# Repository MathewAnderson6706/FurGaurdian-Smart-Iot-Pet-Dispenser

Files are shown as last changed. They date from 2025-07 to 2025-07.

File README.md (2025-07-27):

# Automatic Pet Food Dispensor using RasperryPi 4 
Title Page (1st odd page not numbered, X.0 sections begin on odd pages, otherwise double sided and numbered)  
## Declaration of Joint Authorship   
### Task Distribution
We, FurGuardian, confirm that this breakdown of authorship represents my contribution to the work submitted for assessment and my contribution is my own work and  is expressed in my own words. Any uses made within the Technology Report of the works of any other author, separate to the work group, in any form (ideas, equations, figures, texts, tables, programs), are properly acknowledged at the point of use. A list of the references used is included.
| Task | Mathew | Justin | Tevadi | Zane |
|---|---|---|---|---|
| **3D Print / Container** | 50% | 10% | 10% | 30%  |
| **Mobile Programming** | 30% | 50% | 10% | 10%  |
| **Hardware Connectivity**  | 45% | 25% | 15% | 15%  |
| **Hardware Programming** | 40% | 40% | 10% | 10%  |
| **Documentation** | 25% | 25% | 25% | 25%  |

[^1]
[^1]: Technology Report Guidelines. OACETT, Revised September 2022. Available at: https://www.oacett.org/getmedia/5ad707d7-f472-4b24-a7fe-f34e270b0c41/2022_TR_Guidelines_-_Updated_Version_-_Sept_2022.pdf
## Proposal/Project Specifications   
[Link to proposal](wk01proposal.md).   
## Executive Summary   
Our project focuses on enhancing pet care for owners who are away during the day. It features a **smart pet food dispenser** equipped with advanced functionalities:

- **Camera**:  
  Allow owners to interact with their pets remotely, ensuring constant connection and engagement.

- **Infrared Sensor**:  
  Detects pet presence to automate feeding and interaction processes.

- **Stepper Motor**:  
  Dispenses precise portions of food to maintain proper dietary control.

- **solenoid push intermittent**:  
  Enables treat dispensing as an added feature for rewarding and engaging pets.

## Table of Contents

[Declaration of Joint Authorship](#declaration-of-joint-authorship)   
[Proposal/Project Specifications](#proposalproject-specifications)   
[Executive Summary](#executive-summary)   
[Table of Contents](#table-of-contents)   
[List of Figures](#list-of-figures)   

[1.0 Introduction](#10-introduction)   
[1.1 Background](#11-background)   
[1.2 Project Requirements and Specifications](#12-project-requirements-and-specifications)   
[1.3 Project Schedule](#13-project-schedule)   

[2.0 Hardware Development Platform Report/Build Instructions](#20-hardware-development-platform-reportbuild-instructions)  
[2.1 Mathew Anderson-Saavedra/A](#21-student-onea)  
[2.2 Tevadi Brookes/B](#22-student-twob)  
[2.3 Zane Aransevia/C](#23-student-threec)  
[2.4 Justin Chipman/D](#24-student-fourd)  

[3.0 Mobile Application Report](#30-mobile-application-report)  
[3.1 Deliverable 1](https://github.com/Chipman8472/FurGuardian/blob/master/Docs/FurGuardian_Deliverable1_Group8.pdf)  
[3.2 Deliverable 2](https://github.com/Chipman8472/FurGuardian/blob/master/Docs/Deliverable2/FurGuardian_PetWellness_Group8_2.pdf)  
[3.3 Deliverable 3](https://github.com/Chipman8472/FurGuardian/blob/master/Docs/FurGuardian_Deliverable3_Group8.pdf)  
[3.4 Deliverable 4](https://github.com/Chipman8472/FurGuardian/blob/master/Docs/FurGuardian_PetWellness_Deliverable4_Group8.pdf)   
[3.5 Deliverable 5](https://github.com/Chipman8472/FurGuardian/blob/master/Docs/Deliverable%205/FurGuardian_Deliverable5_Group8.pdf)  

[4.0 Integration](#40-integration)  
[4.1 Enterprise Wireless Connectivity](#41-enterprise-wireless-connectivity)  
[4.2 Database Configuration](#42-database-configuration)  
[4.3 Network and Security Considerations](#43-network-and-security-considerations)  
[4.4 Unit Testing](#44-unit-testing)  
[4.5 Production Testing](#45-production-testing)  
[4.6 Sustainability Considerations](#46-sustainability-considerations)  
[4.7 Challenges/Problems](#47-challengesproblems)  
[4.8 Solutions](#48-solutions)  

[5.0 Results and Discussion](#50-results-and-discussion)

[6.0 Conclusions](#60-conclusions)

[7.0 Appendix](#70-appendix)  
[7.1 Firmware Code](#71-firmware-code)  
[7.2 Mobile Application Code](#72-mobile-application-code)  

[8.0 References](#80-references)  

## List of Figures   
[Figure 1: Gantt Chart](#figure-1-gantt-chart)  

## 1.0 Introduction   
This project was undertaken to complete Humber Polytechnics CENG-355 Captsone project. The problem we are trying to solve is pet owners being away from their animals and not being able to interact or tend to thier needs while away. This dispensor aims to allow users to both interact with and feed thier pets while away from home. 

In section 1 we will discuss similar products on the market, the project requirements and specifications and the project schedule. In section 2 we will discuss the hardware devevlopment of the project. Section 3 links several reports about the development of the mobile app. Section 4 outlines the integration of the project as a whole.
### 1.1 Background
There are a few players on the market already for pet food dispenosrs. Pet Cube offers good remote pet interaction to keep pets engaged but lacks health information for the animals. Whistle offers good health tracking but lacks remote interaction with the animals. Our product aism to fuze these 2 functions into a single product.
### 1.2 Project Requirements and Specifications
This project has the following requirements.

Hardware:
- Raspberrypi 4
- Infared Sensor
- Solenoid push intermittent
- Stepper motor and a controller
- Camera

Firmware:
- Python dependencies (time, threading, cv2, smbus2, socket, RPI.GPIO, flask, pyrebase, pyngrok)
- Compatable python version

### 1.3 Project Schedule       
###### Figure 1: Gantt Chart     
Gantt Chart 

## 2.0 Hardware Development Platform Report/Build Instructions   
### 2.1 Mathew Anderson-Saavedra/A
[Hardware report](hardware/ceng317reportMathew.md)   
### 2.2 Tevadi Brookes/B   
[Hardware report](hardware/ceng317reportTB.md)   
### 2.3 Zane Aransevia/C   
[Hardware report](hardware/rc522.md)  
### 2.4 Justin Chipman/D   
[Hardware report](hardware/ceng317report.md)   
  
## 3.0 Mobile Application Report   
### 3.1 Deliverable 1
[Mobile Deliverable 1](/tree/main/docs/Deliverable%201)   
### 3.2 Deliverable 2      
[Mobile Deliverable 2](/tree/main/docs/Deliverable%202)   
### 3.3 Deliverable 3      
[Mobile Deliverable 3](/tree/main/docs/Deliverable%203)   
### 3.4 Deliverable 4      
[Mobile Deliverable 4](/tree/main/docs/Deliverable%204)   
### 3.4 Deliverable 5      
[Mobile Deliverable 5](/tree/main/docs/Deliverable%205)   

## 4.0 Integration   
This secion will outline the various parts of our project being integrated together.
### 4.1 Enterprise Wireless Connectivity   
### 4.2 Database Configuration   
Our database is a realtime database using Firebase. We use the database to store feeding schedules, pet documents, login credentials, and remote connection URLs. The feeding schedules is fetched and stored locally on the Raspberrypi only being updated when the database signals there is a change. This allows the dispensor to still function without wifi if there is an outage. The pet documents are stored via the app for so the user has a one stop location for all its pets important information. The login credentials are stored in the database so that individual user data does not overlap and it can support more than one user.
### 4.3 Network and Security Considerations   
In this version of the project we are using a tunneling method to tie the raspberrypi's local ip on port 5000 to a public URL so that it can be accesses over other networks. In a production version I would ideally shift to a secure sever so that the feed is less accessable to the public. 

The passwords of the users are not stored in plain text in case of breaches. In future possible encrypting the email would increase security. 
### 4.4 Unit Testing   

### 4.5 Production Testing   
### 4.6 Sustainability Considerations
The controllers of the solenoid and the stepper motor require thier own individual power supply so they are supplied by either a battery or a seperate power adapter. This is not convinient and requires more powers sources than neccessary. 

A suggestion for future improvement would be creating a seperate PCB that can power all components with one adapter, this would make the project more sustainable.
### 4.7 Challenges/Problems   
- A major issue we had was getting the remote connection to be available accress other networks. 
### 4.8 Solutions   
- We created a tunneling method to allow the connection to be more available.
## 5.0 Results and Discussion   

## 6.0 Conclusions   

## 7.0 Appendix
### 7.1 Firmware Code   
[Link to firmware](hardware/firmware).
### 7.2 Mobile Application Code   
[Link to GitHub repository for app]()

## 8.0 References   
[COM-15093 Datasheet](https://mm.digikey.com/Volume0/opasdata/d220001/medias/docus/306/COM-15093_Web.pdf)

[ROB-11015 Datasheet](https://cdn.sparkfun.com/datasheets/Robotics/ZHO-0420S-05A4.5%20SPECIFICATION.pdf)

[Qwiic Relay Python Library](https://github.com/sparkfun/qwiic_relay_py/tree/main)

[AK9753 Datasheet](https://cdn.sparkfun.com/assets/6/7/9/8/e/AK9753_DS.pdf)

[sumbus2 Library](https://github.com/kplindegaard/smbus2)

[Qwiic_Human_Presence_Sensor_Breakout_AK9753 Github](https://github.com/sparkfun/Qwiic_Human_Presence_Sensor_Breakout_AK9753)

[Qwicc Motor Driver Guide](https://learn.sparkfun.com/tutorials/hookup-guide-for-the-qwiic-motor-driver#troubleshooting)

[Qwicc Motor Driver Python Library](https://github.com/sparkfun/Qwiic_SCMD_Py)

[Stepper Motor Datasheet](http://www.sparkfun.com/datasheets/Robotics/SM-42BYG011-25.pdf)

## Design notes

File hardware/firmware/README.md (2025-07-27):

# Firmware directory
- **presence_cam_stream.py** is our working firmware that polls our human presence detector and initiates a stream via local ip. The code then updates the firebase with the address for the stream and keeps it open until the presence is gone.
    - **Current Issues**: The stream leaves the last image open when presence is left. The IR readings are heavily influences by its surroundings. Need to figure out a way to dynamically create a threshold. As of now it is manually changed to enviroment.
- **date.py** is our food scheduling code that retrieves schedule information from the DB and dispenses food according to the provided schedule. It maintains a constant connection with the DB to monitor for changes to the schedule.
    - **Current Issues**: A temperary fix of a boolean value is put into the database to prevent the motor from dispensing for the whole minute.

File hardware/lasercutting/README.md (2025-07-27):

# Laser Cutting
1. In comparison to 3D Printing (scad and exported stl files in the repository), laser cutting is much faster.
2. Software access off campus or on a laptop: myapps-> app stream-> Adobe Illustrator
3. Use Adobe Illustrator to create a .ai file and add that plus the associated exported pdf file to the repository.
- Red for inside cuts, green for outside cuts, blue for vector engrave, black for raster etch.
- Get your design cut at [The Built Environment Labs - N114A Laser Cutting Lab](https://designandbuiltlabs.simplybook.me/v2/#book/category/2/service/11/count/1/) Tuesdays 9-3, other weekdays 8-4. Email your .ai design's .pdf equivalent to fastlasercutter@humber.ca letting them know that you are a Computer Engineering Technology student and that it is for the encloure assignment in CENG 317 Hardware Production Technology. Ask them to please cut it out of clear 3mm acrylic letting them know to please give you at least 8 of the donut/spacers. Pick it up 4 days after submitting it or sooner.   

### To invert Sparkfun images
1. Open in paint.
2. Select all.
3. Right click.
4. Select Invert selection/color.
5. Ctrl-C in Paint, Ctrl-V in Adobe Illustrator.
6. Right click and choose Order->Send to back of page.

### To import sch/brd files
1. Download both the sch and brd files.
2. Import the Eagle files in KiCad. (File->Import non-KiCad Project->EAGLE project)
3. Auto match the layers.
4. Print the brd to pdf. (All or just Edge.Cuts and F.Adhesive?)
5. Open the pdf with Adobe Illustrator.
6. Cut and paste the portions that you want, remember to remove the fill for the mount holes and add an outline.
7. Right click and choose Order->Send to back of page.

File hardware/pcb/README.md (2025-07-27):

# KiCad   
1. We will be designing a Raspberry Pi Interface board using [KiCad 8.0.3](https://downloads.kicad.org/kicad/windows/explore/stable/download/kicad-8.0.3-x86_64.exe).
2. Chapter 18 of the below textbook on pages 259-284, pages 268-293 of the pdf, has Project 2: Design a small Raspberry Pi HAT.
   Dalmaris, Peter. (2018). KiCad Like a Pro 2nd edition. United Kingdom: Elektor International Media B.V. Tech Explorations: EBOOK SOLO 978-1-64440-886-5. Note that newer versions of the textbook do not include the Design a small Raspberry Pi HAT project.   
3. Launch KiCad:   

4. Start with default settings:   

5. I have followed [Using a template](https://techexplorations.com/guides/kicad/3e/create-a-new-kicad-project-from-a-template/) and [Vlad's guide to PCB facilities in J233](PCBPrototypes.md) to a certain extent in order to create the below files to start from:
-   [Project File](/hardware/pcb/StudentName2023-11-08.kicad_pro)
-   [Schematic File](/hardware/pcb/StudentName2023-11-08.kicad_sch)
-   [PCB File](/hardware/pcb/StudentName2023-11-08.kicad_pcb)   
6. Download the above /hardware/pcb/StudentName2023-11-08.kicad_pro, pcb, and sch.
7. Use KiCad to open the _pro project file, then navigate to opening the PCB file.
8. Change the board in the PCB view to have your name and the current date.
9. If not routed already, route the BJT as a switch circuit (Section 4.5 Page 192 in your Electronic Devices by Floyd) traces on the PCB. This involves a 2N4124 NPN transistor with a 2.2 kOhm resistor between pin 11 -- GPIO17 and the base of the transistor, connect the emitter to the ground, and connect an LED with a series 220 Ohm resistor on the collector side to 3.3V. To do this:   
   - Click on the the end of say a resistor and press 'x' on the keyboard.
   - Then click on the other terminal that it should be connected to.
   - Consider ease of soldering.
10. Add a PinHeader_1x03_P2.54mm_Horizontal near the edge of the board to be able to connect a micro servo to pin 33 -- GPIO13, 3.3V (middle pin), and GND.
11. Add an extra Conn_01x08_Female that makes it possible to connect to the signals that we use for I2C (3V3,GND,SDA,SCL), the LED (GPIO17), a possible micro servo (GPIO13), and 2 extra connections.
12. Consider widening the traces where possible to reduce the likelihood of lifted pads/traces.   
13. Save "project as" what you changed the name and date to.   
14. Use File->fabrication outputs->Gerbers (.gbr)... to Plot the Gerbers   
15. also "Generate Drill Files"->PTH and NPTH in single file   
16. Save project
17. Use the Gerber Viewer to preview:
    1. F_Cu.gtl
    2. B_Cu.gbl
    3. F_Silkscreen.gto
    4. B_Silkscreen.gbo
    5. F_Mask.gts
    6. B_Mask.gbs
    7. Edge_Cuts.gm1
    8. .drl    
18. Upload your work in a zip file to your /hardware/pcb/ folder in the PrototypeZone organisation. The name of the zip should be in the format of your changed name and date (StudentName2023-09-24.zip) and it should contain the 3 KiCad files you worked on, the combined drill file, and the default Gerber plots as per the following list:   
    1. F.Cu   
    2. B.Cu   
    3. F.Silkscreen   
    4. B.Silkscreen   
    5. F.Mask   
    6. B.Mask   
    7. Edge.Cuts   
    8. The drill file   
    9. Your _pro file   
    10. Your _sch file   
    11. Your _pcb file
19. Once the professor knows that your zip file has been uploaded correctly they will send the class set to the lab next door to be made [in house](/hardware/pcb/PCBPrototypes.md).
20. When the completed PCB is available, proceed to [inspect it](/hardware/pcb/inspection.md).
21. Further iterations of the board can be made [in house](/hardware/pcb/PCBPrototypes.md) or by [OSHpark](https://oshpark.com/),  [MicroArt](https://microart.pcborders.com/), [Bittele](https://onlinequote.7pcb.com/), [JLC](https://jlcpcb.com/), [PCBway](https://www.pcbway.com/QuickOrderOnline.aspx), [Seeedstudio](https://www.seeedstudio.com/fusion_pcb.html), or other alternatives.

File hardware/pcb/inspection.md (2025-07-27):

# Pre-soldering Inspection
1. Visual Inspection:   
Inspect the PCB for any visible shorts or copper imperfections from the production process.
Check for any damage to the traces, or PCB.
2. Power and Ground:   
Ensure that the power and ground connections are correctly established for all components.
Verify that the power supply voltage matches the requirements of the components.
3. Continuity Test:   
Use a multimeter's continuity mode to verify the above and that there are no open circuits/breaks, or shorts in the
traces.
4. Consult Documentation:   
Refer to datasheets and technical documentation for components to ensure correct usage and
connections.
5. Component Orientation:   
Double-check that all components, including the LED and transistor are
correctly oriented.
6. Consider the [Safety Data Sheet](https://aimsolder.com/sites/default/files/alloy_sac305_ws482-ghs_america-english.pdf)   
7. Proceed to reduce the amount of oxide on the PCB by using a [3M Scotch-Brite cleaning pad](https://en.wikipedia.org/wiki/Scotch-Brite).   
8. If all is well, proceed to begin with surface mount components followed by through hole components.
# Space constraints
1. The LED should be on its side as per the KiCad PCB design file.   
2. Please note that for the transistor you only have about 1 cm of space.   
   
# Post-soldering Inspection Process adapted from BioBytes
1. Visual Inspection:
Inspect the soldered connections, components, and PCB for any visible solder bridges, cold
solder joints, or misplaced components.
Check for any damage to the components, traces, or PCB.
2. Power and Ground:
Ensure that the power and ground connections are correctly established for all components.
Verify that the power supply voltage matches the requirements of the components.
3. Consult Documentation:
Refer to datasheets and technical documentation for components to ensure correct usage and
connections.
4. Component Orientation:
Double-check that all components, including the LED, sensors/effectors, and resistors, are
correctly oriented and soldered in the right positions.
5. Soldering Quality:
Reheat any suspicious solder joints to ensure proper bonding and conductivity.
Remove excess solder or solder bridges with a soldering iron and desoldering wick.
6. Continuity Test:
Use a multimeter's continuity mode to verify that there are no open circuits or breaks in the
traces.
Test the continuity of connections between the components and their corresponding pins on the
PCB.
7. Signal Integrity:
Check if the GPIO pins on the Raspberry Pi are correctly connected to the LED and sensor/effector.
Use a multimeter or oscilloscope to verify that the signals are reaching the correct pins.
8. I2C Communication:
Verify the I2C communication between the Raspberry Pi and the sensor/effector.
Check the sender's address and the Raspberry Pi's I2C settings in the software code.
9. Code Inspection: Scrutinize code for errors and logic flaws.
10. LED Behavior:
If the LED is not blinking as expected, review the software code controlling the LED.
Confirm that the GPIO pin settings and blinking pattern are correctly programmed.
11. Sensor Data:
If the LED behaviour is influenced by the sensor or effector's use, ensure that the sensor is
correctly connected and functioning.
Check if the sensor is providing accurate acceleration data to the Raspberry Pi.
12. Component Replacement:
If a component is suspected to be faulty, consider replacing it with a new one and retest the
circuit.
Ensure that the replacement component is of the same type and specifications.
13. Isolation Testing:
Isolate sections of the circuit to identify specific problem areas.
Test individual components or sections of the PCB to pinpoint the source of the issue.
14. Seek External Help:
If the troubleshooting steps prove challenging, seek advice from experienced individuals, online
communities, or forums.
15. Record Changes and Repeat Testing:
Document any changes made during troubleshooting, including component replacements,
adjustments to code, or modifications to connections. After making changes, repeat testing to
verify whether the issue has been resolved.

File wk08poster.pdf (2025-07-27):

# FurGuardian

## Justin Chipman, Mathew Anderson-Saavedra, Tevadi Brookes, Zane Aransevia, CENG 355

### ENCLOSURE DESIGN

We have designed a custom 3D-printed enclosure to securely house the components of our smart pet food dispenser. Engineered for durability and efficiency, the enclosure features a compact structure (102.175 x 201.175 x 140mm) with optimized internal compartments for sensors, motors, and electronics.

The design includes ventilation for heat dissipation, secure mounting points for stability, and a modular layout for easy maintenance. Its sleek and functional form ensures seamless integration into any home environment, enhancing both usability and aesthetic appeal.

INTRODUCTION

We have developed a smart pet care system designed to assist pet owners who are away during the day. Our Internet of Things (IoT) capstone project integrates a distributed computing model with a mobile application, a cloud-connected database, and an intelligent embedded system featuring custom hardware and an enclosure (3D printed/laser cut).

With our project, we have created and implemented a smart pet food dispenser. The key features of our project are a remote webcam feed triggered by an IR sensor, a remotely scheduled food dispenser, and a remotely controlled treat dispenser. With these features we aim to provide pet owners the opportunity to interact and care for their pets while they are away from home.

### CIRCUIT BOARD METHOD

Our custom PCB design allows us to utilize the QWIIC connections with our raspberry pi 4. With this we were able to daisy chain our components together for seamless and reliable connection.

### MOBILE APP RESULTS

On the home screen of our app features the camera feed to the dispenser accompanied by a manual treat and food dispense button. There is a manual feed refresh button in case of feed disruptions.

Our health screen features a time picker that allows you to input scheduled feeding times up to 3 times a day.

Our records screen allows
users to store their pets
records. This could include vet visits, vaccination records, weight, and any other
information the user deems important.
The pet education screen
Features a wide variety
Of categories for users to Scroll in search of the
Information they need.

### DATABASE

- Pet Profile Management: Store detailed pet information, including name, breed, age, medical history, and vaccination records.
- User Authentication: Secure login system using Firebase Authentication, supporting email/password and social logins.
- Real-time Updates: Instantly sync pet data across multiple devices using Firebase Firestore.
- Seamless Server Connectivity for Secure Pet Data Storage.
- User-Driven Updates: Data refreshes instantly when users modify pet profiles.
- Firebase Firestore Sync: Ensures changes are reflected across all connected devices.

### TESTING

- We utilized sunflower seeds as a stand-in for pet food to simulate real-world feeding scenarios.
- Experimented with various dispensing mechanisms to identify the most efficient and pet-friendly method.
- Designed and 3D-printed an inner tube and spiral mechanism to evaluate different food dispensing techniques.

## ACKNOWLEDGEMENTS

Kristian Medri, Idea Lab( 3D Printing), Imran Zafurallah, Vincent Balcita, Clarence Oriola, etc.

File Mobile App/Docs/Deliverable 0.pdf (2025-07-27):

Team Name: FurGuardian

Project Title: Pet Wellness

Group 8: Justin Chipman – N01598472

Imran Zafurallah - N01585098

Zane Aransevia - N01351168

Tevadi Brookes - N01582563

Github ID: JustinChipman8472, ZaneAransevia-n01351168, TevadiBrookes2563, ImranZafurallah5098

Topic: Pet wellness app

Problem:
Caring for a pet goes beyond simply being present at home; it involves continuous attention to their health and well-being. However, many pet owners struggle to consistently monitor their pets' needs, whether they are home or away. Existing solutions, like apps that provide pet-sitting services, only address temporary care needs. There is a growing need for a comprehensive tool that supports pet wellness and health management at all times.

Solution:
Our app aims to provide a holistic, continuous approach to pet care, offering tools that help owners manage every aspect of their pet’s wellness around the clock. Key features include:
- Health Monitoring: The app will track critical health markers such as activity levels, weight, hydration, and eating habits, providing insights that help owners keep their pets in optimal health.
- Medical Record Management: A digital vault will store all pet medical records, making it easy to access and share with veterinarians, ensuring up-to-date care.
- Remote Feeding: An autonomous food dispenser will allow owners to schedule or feed their pets at any time, whether at home or remotely.
- Live Monitoring and Interaction: Owners can watch live video streams of their pets and interact with them using two-way audio, helping them stay connected even when in different rooms or outside the home.
- Wellness Alerts: The app will send timely reminders and alerts for things like feeding schedules, medication, or even recommended activities based on health data.

By offering continuous monitoring, feeding, and health tracking, our app supports pet wellness at all times, ensuring that pets’ needs are met whether their owners are with them or not.

Sensors: Human Detection IR sensor – used to make sure only pets are recognized.

DC motor – used to dispense the pet food

RFID sensor – used to detect and differentiate between multiple pets.

Liquid Level Sensor – used to detect if the pets water level is low.

Heart rate sensor – used to detect the pets heart rate.

Scale – to weight food.

Camera + microphone – for interacting with pets.

Plan to Collaborate: We plan to split the project into different features of the app and have a meeting with each other 2 times a week. With each person overseeing coding a feature we then come together during the meetings and discuss challenges we are having and consult the other group members for help.

We are adapting the app on android because android dominates the global market with over 70% market share. It is an open-source platform and has lower entry cost barriers. Developing an android app also means our app can run on a wide range of devices from budget phones to high end models.

Yes, we have considered making a google play account. First, we would make a google account and then go to sign up for a developer account and pay the one time $25 fee. Then we would fill out our developer profile and complete the registration.

Android development skills: Justin Chipman – 10

Imran Zafurallah – 8

Zane Aransevia – 9

Tevadi Brookes – 8

Collaboration so far: The team has spent hours working remotely via Discord with each other. We discussed many different ideas for our software app and ultimately found a common interest in a pet wellness app. From there we discussed how we would apply our hardware in the future for project and what additional feature we could include to make the application really stand out from the rest. All group members have suggested very viable and feasible ideas such as pet food sale notifications, Cameras to see the pet while not home, RFID tags to identify specific animals, etc.

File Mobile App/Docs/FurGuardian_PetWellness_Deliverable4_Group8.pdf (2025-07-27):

# Deliverable 4

Team Name: FurGuardian

Project Name: Pet Wellness App

Team Group: 8

Student Names and ID’s: Justin Chipman – N01598472

Imran Zafurallah - N01585098

Zane Aransevia - N01351168

Tevadi Brookes - N01582563

Name | Student Id | Github Id | Signature | Effort
Justin Chipman | N01598472 | Chipman8472 | Justin C | 100%
Imran Zafurallah | N01585098 | ImranZafurallah5098 | Imran Z | 100%
Zane Aransevia | N01351168 | Zayine917 | Zane A | 100%
Tevadi Brookes | N01582563 | TevadiBrookes2563 | Tevadi B | 100%

GitHub Link: https://github.com/Chipman8472/FurGuardian.git

Issue FurGuardian solvesG

FurGuardian addresses the market’s lack of comprehensive pet wellness solutions by integrating health, activity, and interaction features into a single platform. It solves the problem of fragmented pet care by offering a centralized way for pet owners to manage health records, track fitness, and monitor wellness insights, ensuring pets receive optimal care. Additionally, FurGuardian provides tailored health tips and real-time tracking (planned) to address potential health issues proactively.

Comparison of two apps with FurGuardian

Pros and Cons:

- PetCube:
- Pros:
■ Great for remote pet interaction (camera, treats, audio).
■ Offers fun and engaging features like live streaming and treat dispensing. ■ Well-suited for entertainment and keeping pets engaged.
- Cons:
■ Lacks detailed health records or medical history.
■ No fitness tracking or activity monitoring beyond interaction. ■ Does not offer pet wellness insights or health tips.
- Whistle:
- Pros:
■ Excellent for GPS tracking and activity monitoring.
■ Provides insights into pet activity, sleep patterns, and overall fitness. ■ It is ideal for tracking physical health and pet safety.
- Cons:
■ No interaction features (camera, treats).
■ Does not track detailed health records or offer health tips.
■ Limited to fitness and safety, it lacks comprehensive wellness features.
- FurGaurdian:
- Pros:
■ Comprehensive health management: Tracks fitness, activity, health records, and wellness tips.
■ Ability to manage pet profiles with medical history, vet visits, and more. ■ Planned features like device control (e.g., treat dispenser, food schedule).
■ Real-time tracking and tailored health tips.
■ We are focused on holistic pet care, blending health monitoring and interaction.
- Cons:
■ No GPS tracking (unless integrated with external devices).
■ Device control is still a planned feature (not yet implemented).
■ Relies on user input for health metrics (e.g., weight) rather than real-time automated data.

Feature/Aspect | PetCube | Whistle | FurGuardian
Main Focus | Pet interaction (camera, treats, audio) | GPS tracking and activity monitoring | Comprehensive pet health and wellness management
Pet Interaction | ✔️ Two-way audio, treat dispensing, camera streaming | ❌ No remote interaction features | ✔️ Planned features for device control (e.g., food dispenser)
Activity Tracking | ✔️ Monitors pet movement, interaction | ✔️ Tracks physical activity (steps, playtime, sleep) | ✔️ Activity tracking (steps, weight, hydration, etc.)
Health Records | ❌ No detailed health records or vet visit tracking | ❌ Limited health records | ✔️ Detailed health records, vet visits, medical history
GPS Tracking | ❌ No GPS tracking | ✔️ Real-time GPS tracking for pet location | ❌ No built-in GPS tracking
Health Tips | ❌ No health tips | ❌ No health tips | ✔️ Tailored health tips, including weight management
Pet Profiles | ❌ Limited to interaction features | ✔️ Basic pet profile (focus on activity) | ✔️ Detailed pet profiles with breed, medical history, etc.
Device Control | ✔️ Treat dispensing, camera interaction | ❌ No device control | ✔️ Planned control of pet devices (e.g., food dispenser)
User Experience | ✔️ Interactive and engaging | ✔️ Focused on fitness tracking | ✔️ Comprehensive wellness, health records, and activity logs
Real-Time Health Tracking | ❌ No real-time health metrics | ❌ Limited real-time health tracking | ✔️ Planned real-time health tracking (heart rate, hydration)
Pet Wellness Insights | ❌ No wellness insights | ❌ Limited wellness insights | ✔️ Health and fitness insights based on tracked data

Battery & Alerts ✔️ Alerts for device status

✔️ Alerts for battery
life and activity
changes

✔️ Alerts for health
updates and pet status
Cost | 💸 Higher device cost (camera and treat dispenser)

💸 Device cost for
GPS tracking collar

💸 No cost

FurGuardian stands out as the best option due to its comprehensive health and wellness features, including tracking fitness, activity and maintaining detailed health records like vet visits and medical history. It offers tailored health tips, wellness insights, and planned real-time health tracking, providing a holistic approach unmatched by competitors. Unlike PetCube and Whistle, Furguardian supports detailed pet profiles, allowing owners to manage breed, medical history, and other vital information. Combining health monitoring, planned device control, and interaction features bridges the gap between wellness and engagement, making it ideal for overall pet care. Its app-based solution is also more cost-effective, avoiding the expensive devices required by competitors. With plans for smart device integration, FurGuardian continues to evolve as a forward-thinking and comprehensive pet wellness platform.

### What we did this sprint

Justin:
I worked on implementing the hashing algorithm to encrypt the passwords before being stored into the database. This way the account passwords are not displayed in plain text in our database. I also worked on fixing our PetEdFragments performance issues. It was loading very slow and even crashing our app sometimes. I found that the cause of our issue was heavy sequential processing needed in the creation of the fragment between the geocoder and the webview. My solution was to implement multithreading so that the components can be initialized in parallel. In terms of the crashing I found many uncaught exceptions especially with requireContext() calls. So I simply handled them accordingly to fix the crashing. As well I updated the feedback functionality to incorporate more input handling and graying out the submit button for 24 hours preventing one user from flooding our feedback potentially diluting our data findings later on. Another aspect of the app I worked on this sprint was unit testing. I implemented 10 tests for LoginActivity to ensure sharedprefs, proper intent transfer and other crucial components functioned correctly.

Tevadi:
In this sprint I improved on the Records fragment completely changing the layout, implemented a pet medical record management system that was integrated with Firebase Realtime Database. The Records Fragment was changed to dynamically display medical records and a button for retrieval of that data. A RecordsAdapter was created to bind the Firebase data to a custom card layout called card medical records(xml), displaying specific details about that pet’s record with functionality to delete records. Troubleshooting steps were taken to resolve issues with unresolved IDs and missing resources ensuring proper linkage between layouts and code. The final implementation successfully integrates Firebase for data storage and retrieval, dynamically displays records and provides functionality to manage and add new medical records. I also worked on the creation of the C4 Model “System Context Diagram” and the “Container Diagram”.

Imran:
This Sprint I worked on the PetEd fragment to optimize it and redid the fragment layout and introduce the spinner class with webview for a full integration. The PetEd fragment will now open the web pages and youtube videos within the app and only take you out if you need to make a schedule for vaccinations or check up within the calendar app, all other activities are done within the app for convenience and simplicity.

+
Zayne:
I collaborated with Tevadi in redesigning the records fragment. We ran into some issues with not being able to store an actual file without paying for firebase storage. So for the meantime we implemented just text and dates for the records.

### Sprint Goals

Increase account security
Write unit tests for LoginActivity
Modify simulated data to mimic more realistic behavior Relieve technical debt in PetEdFragment
Improve RecordFragment Design

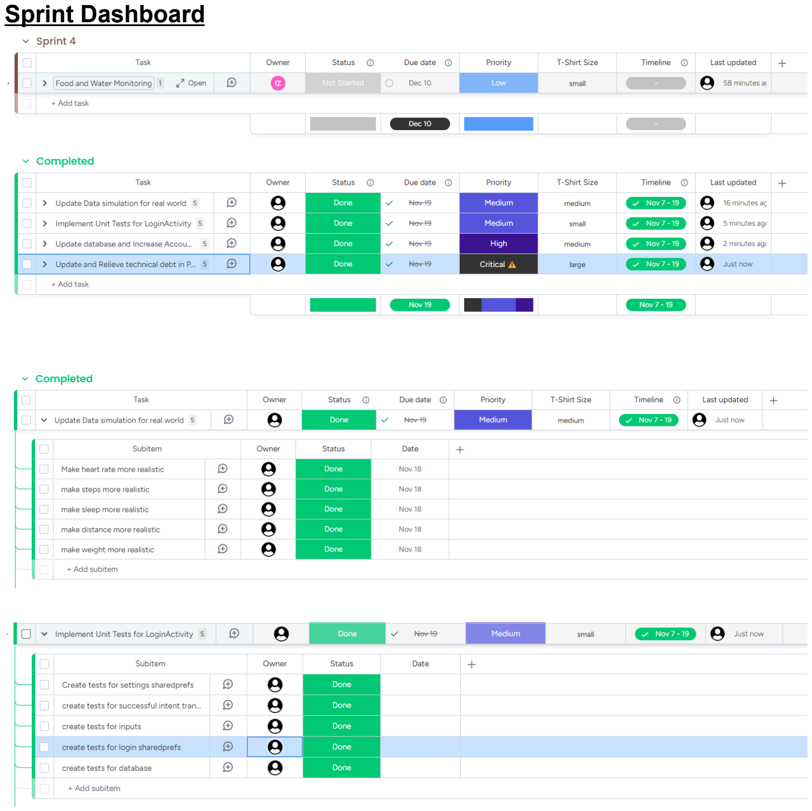
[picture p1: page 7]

### Sprint Dashboard

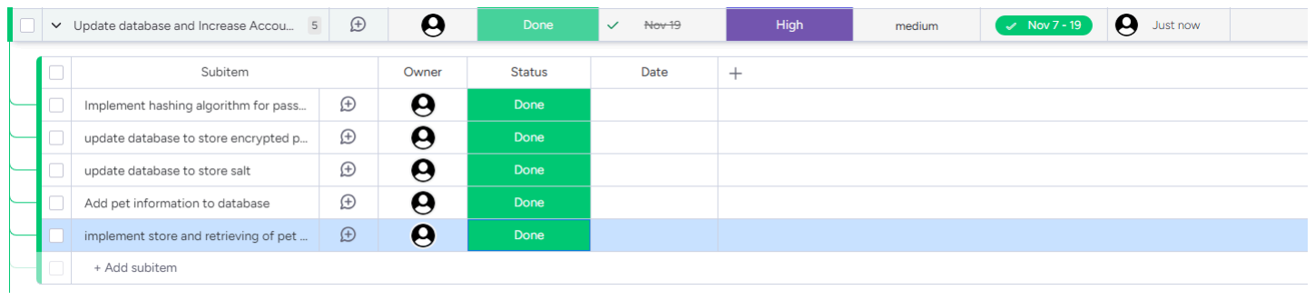
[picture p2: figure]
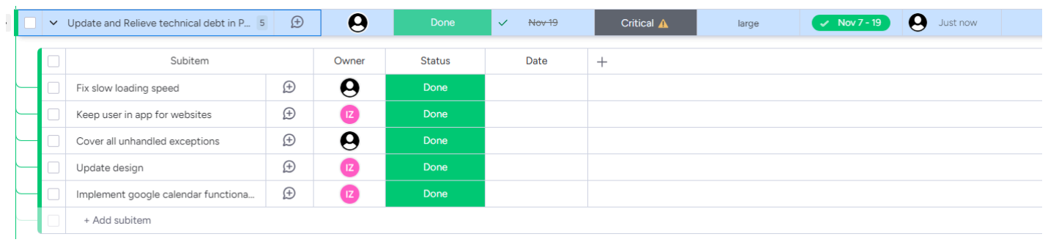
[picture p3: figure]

### Team Discussions

Our discussions were mostly voice call based so here is three screenshots of different voice call dates of our group.

topics discussed:
Improving petEd fragments performance
updating record fragment design implementing encryption for our passwords increasing our error handling

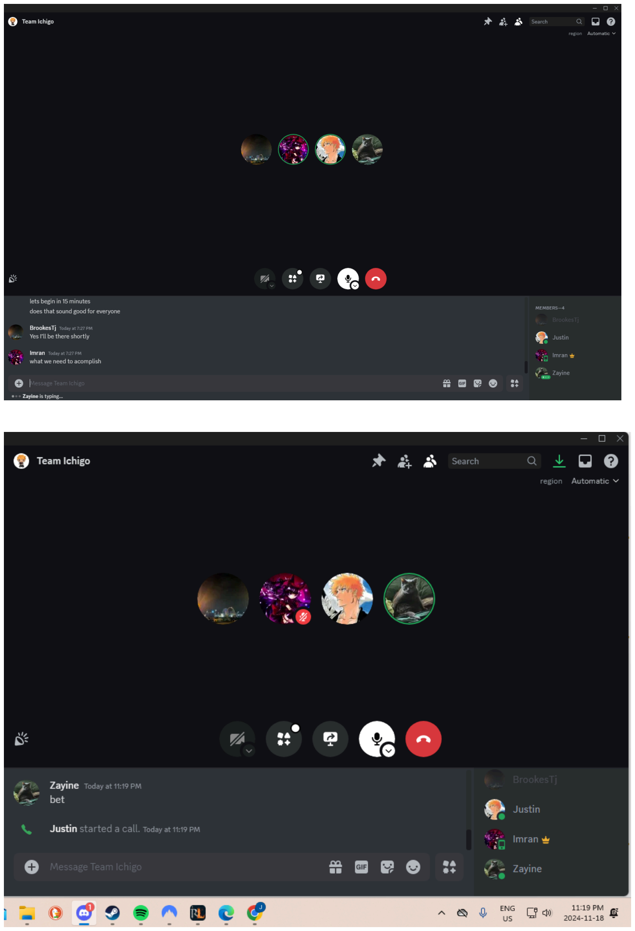
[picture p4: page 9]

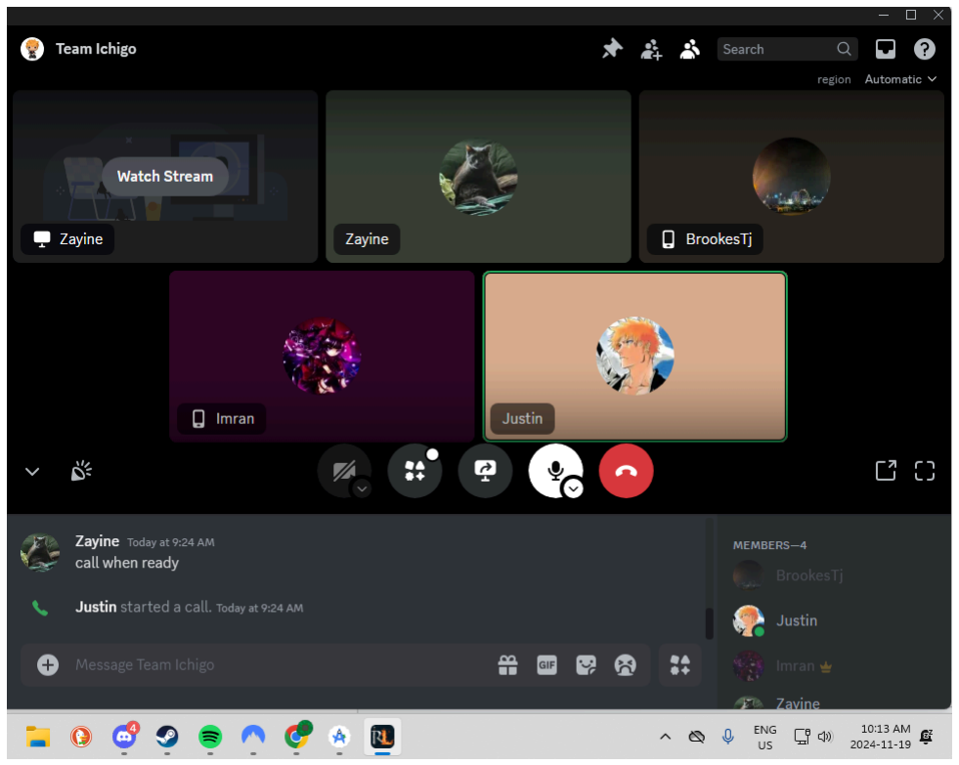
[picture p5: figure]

### Sprint Retrospective

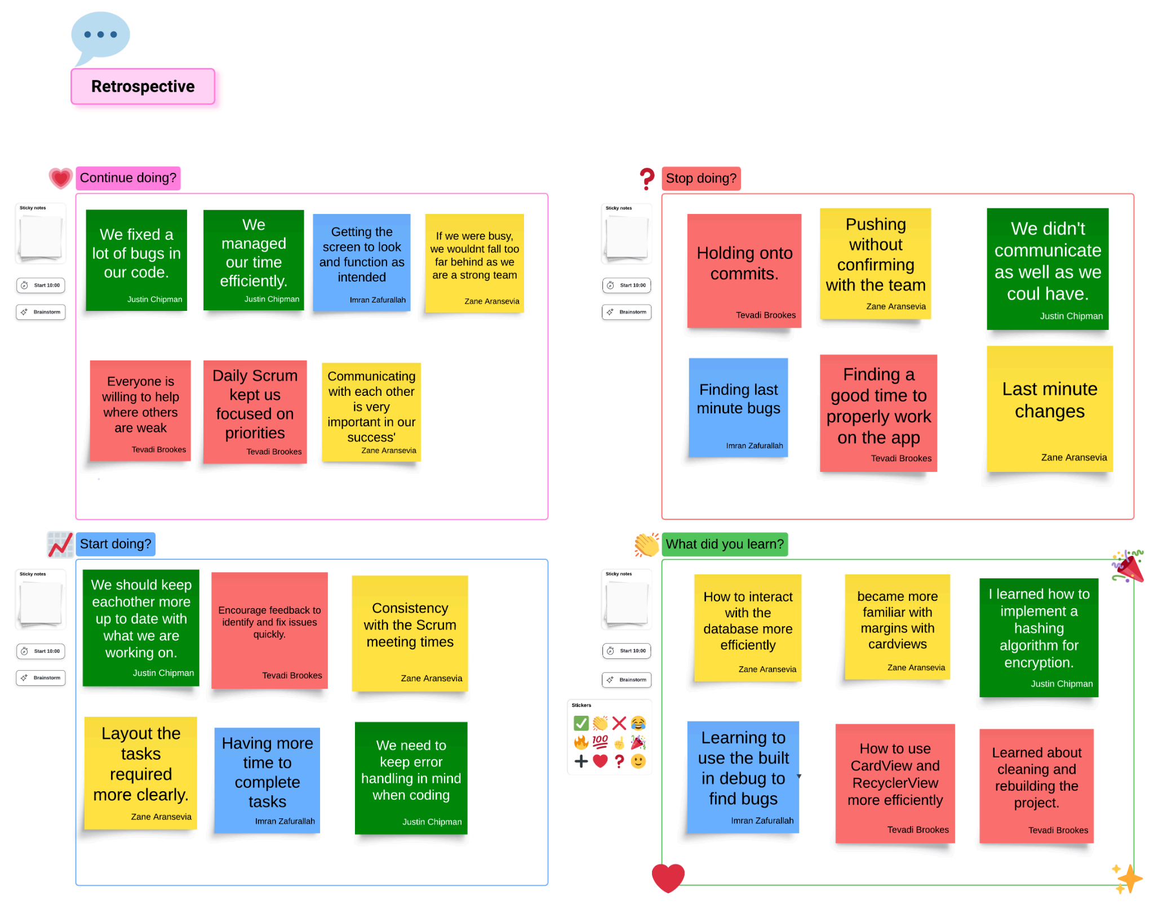
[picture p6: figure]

### C4 Model System Context Diagram

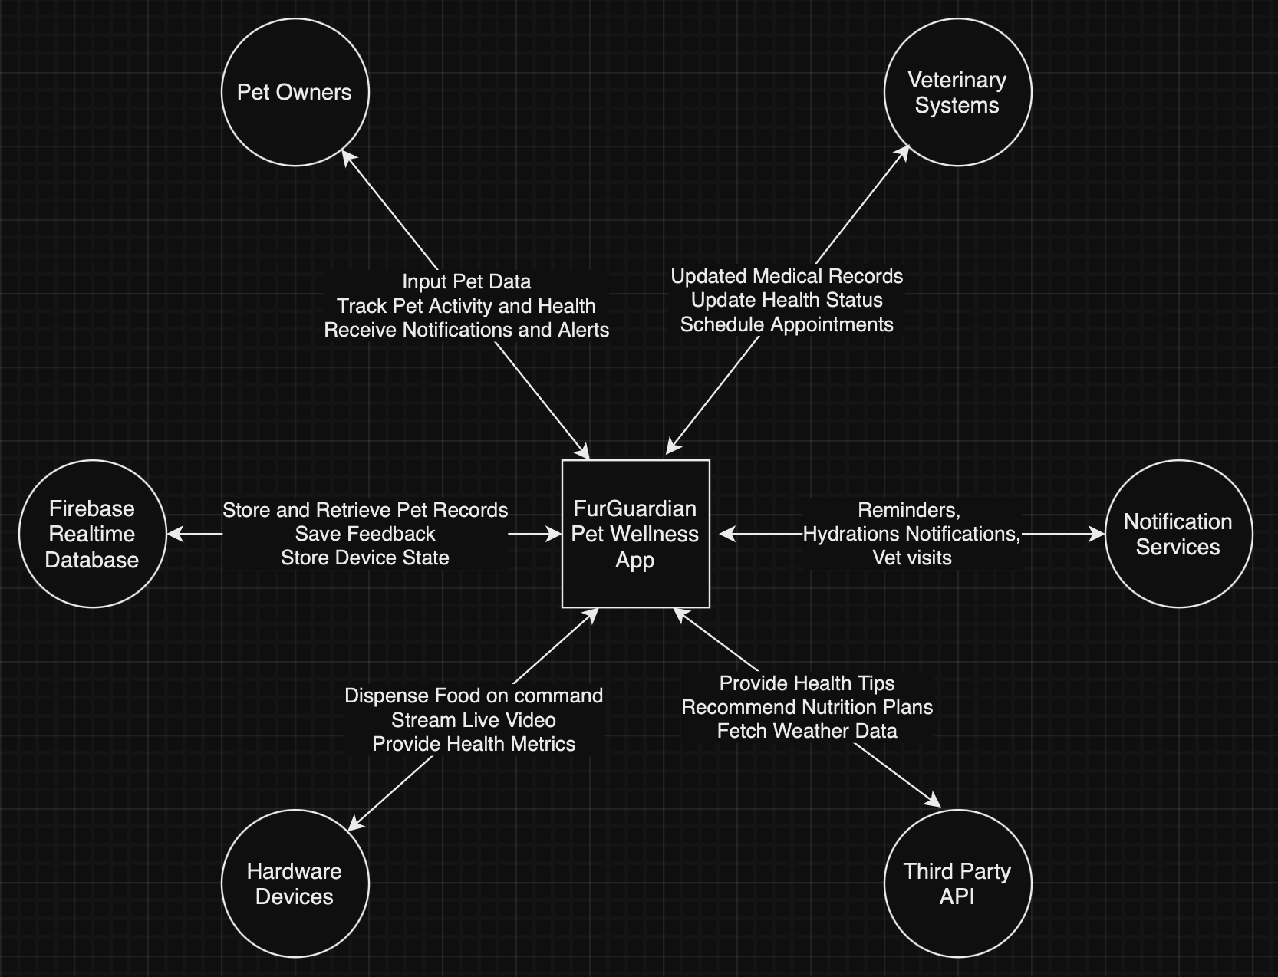
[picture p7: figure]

### C4 Model Container Diagram

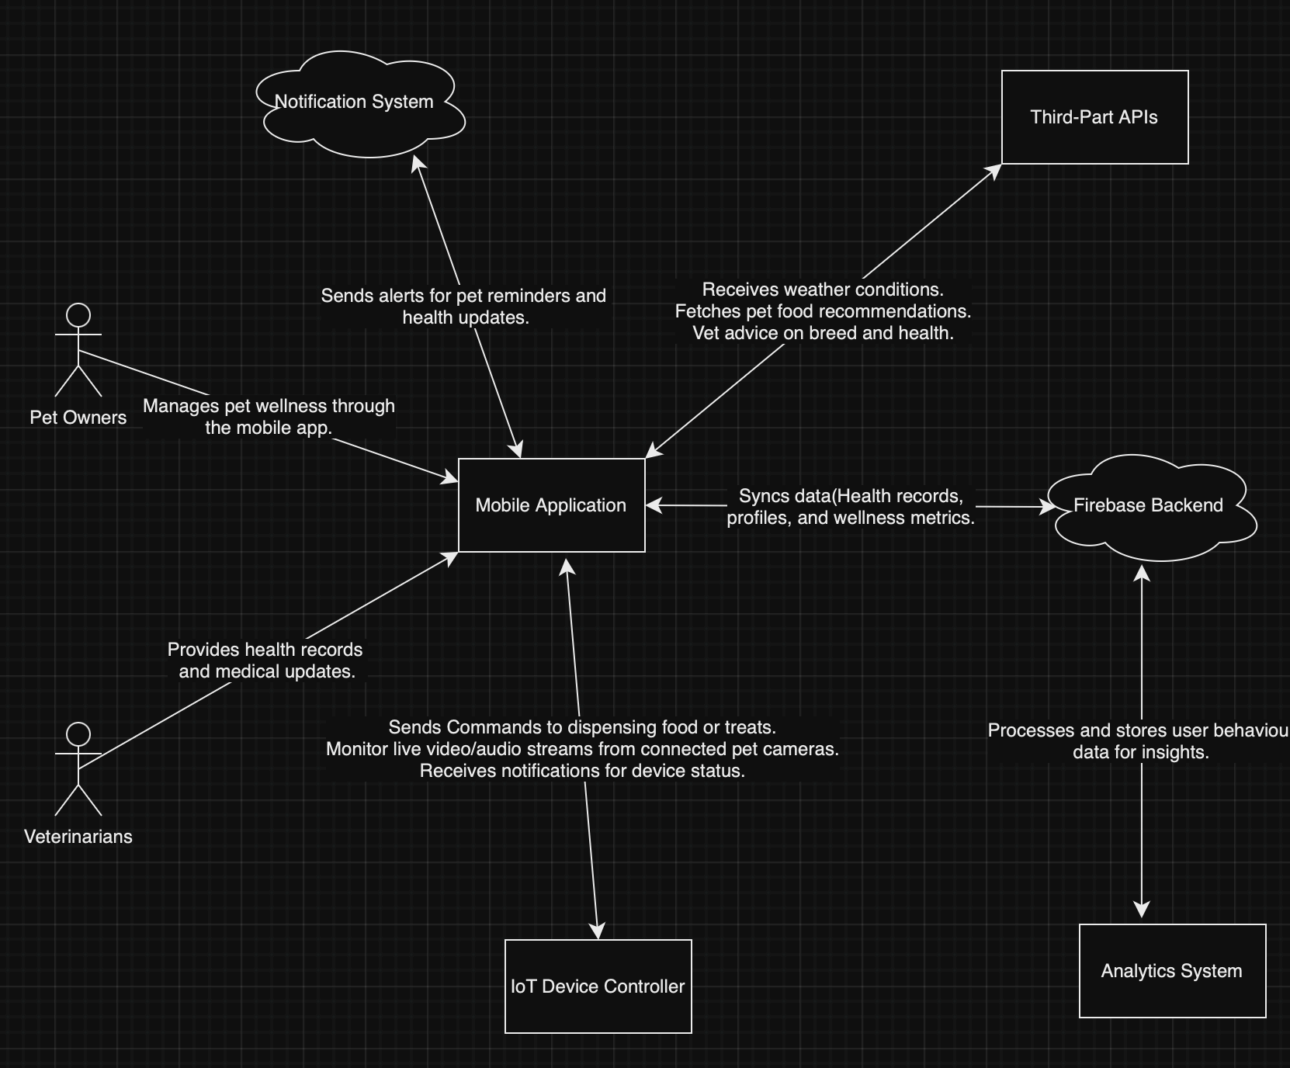
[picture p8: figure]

### Design Patterns

Singleton
public UserModel() {
FirebaseDatabase database = FirebaseDatabase.getInstance(); this.usersRef = database.getReference("users");
}

Here we demonstrate the use of a singleton object. Since we don't want to create multiple instances of our database connection we use getInstance() so that if there is a connection already opened we access that one instead of making a new one.

Builder
// Show success dialog
new AlertDialog.Builder(requireContext()) .setTitle("Thank You!")

.setMessage("Your feedback has been submitted successfully!") .setPositiveButton("OK", (dialog, which) -> resetFields()) .setCancelable(false) .show();
}, 2000);

Here we demonstrate the use of the builder design pattern. Which is used to build the alertdialog piece by piece and allowing us to choose what features we want to add. This is the benefit of the builder pattern: it allows for the same building process to produce different products.

### Test case screenshot

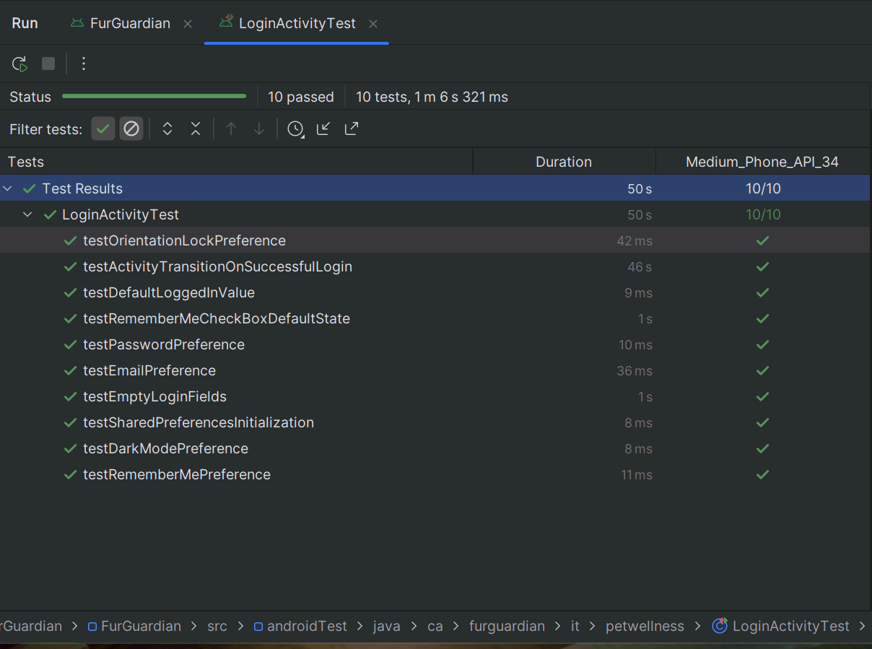
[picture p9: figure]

### Data being stored in Database

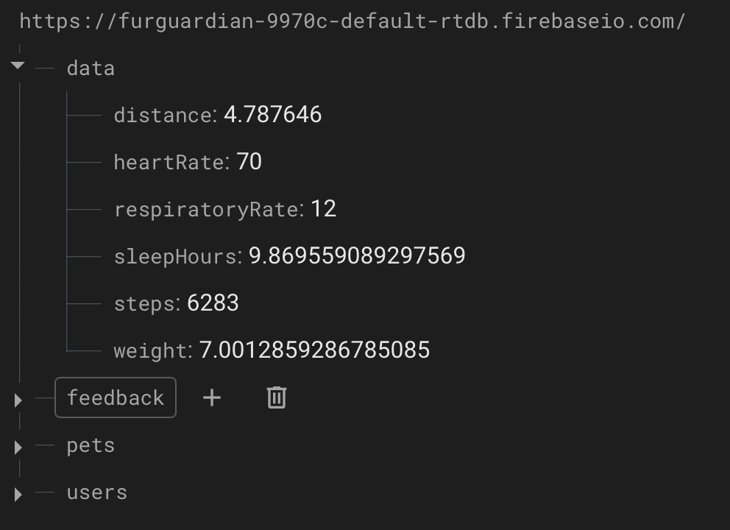
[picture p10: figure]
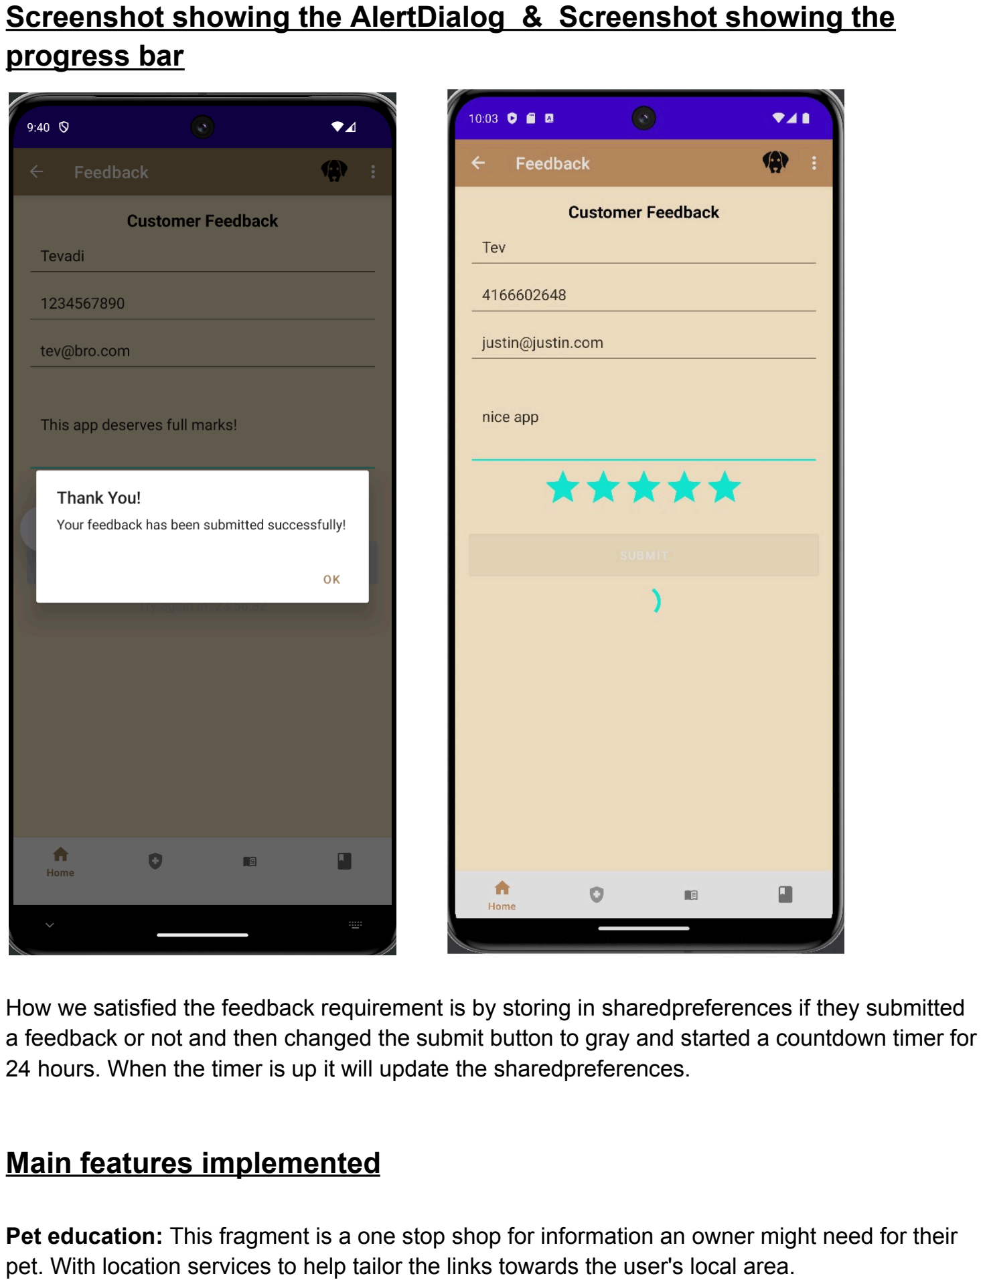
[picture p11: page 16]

### Screenshot showing the AlertDialog & Screenshot showing the progress bar

How we satisfied the feedback requirement is by storing in sharedpreferences if they submitted a feedback or not and then changed the submit button to gray and started a countdown timer for 24 hours. When the timer is up it will update the sharedpreferences.

### Main features implemented

Pet education: This fragment is a one stop shop for information an owner might need for their pet. With location services to help tailor the links towards the user's local area.

Health: This fragment actively communicates with the stored sensor data from the database and displays it. It also gives recommendations based on the read data. (i.e. go for a walk, get some more sleep, etc.)

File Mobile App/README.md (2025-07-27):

# FurGuardian App

## Intro
This app is used to interact with our remote monitoring and pet food device. 

### Team Members
Justin Chipman – N01598472
Imran Zafurallah - N01585098
Zane Aransevia - N01351168
Tevadi Brookes - N01582563
Mathew Anderson-Saavedra - N01436706

### Project Overview
The FurGuardian app is a comprehensive pet wellness platform designed for Android. 
It offers real-time pet monitoring, health tracking, feeding schedule management, and access to medical records. 
The app's user-friendly interface integrates cutting-edge technology like live video streaming, heart rate sensors, 
and remote food dispensing, making it easier for pet owners to care for their pets anytime, anywhere.

### Features
**Live Monitoring:** Stream live video and audio from your pet's environment, allowing real-time interaction.
**Health Monitoring:** Track key health metrics like heart rate, hydration, and activity levels.
**Feeding Schedule:** Remotely schedule and dispense food, check water levels.
**Medical Records:** Access your pet’s vaccination history, medical records, and more.
**Insights:** Educational content about pet care and nutrition.

### Project Image
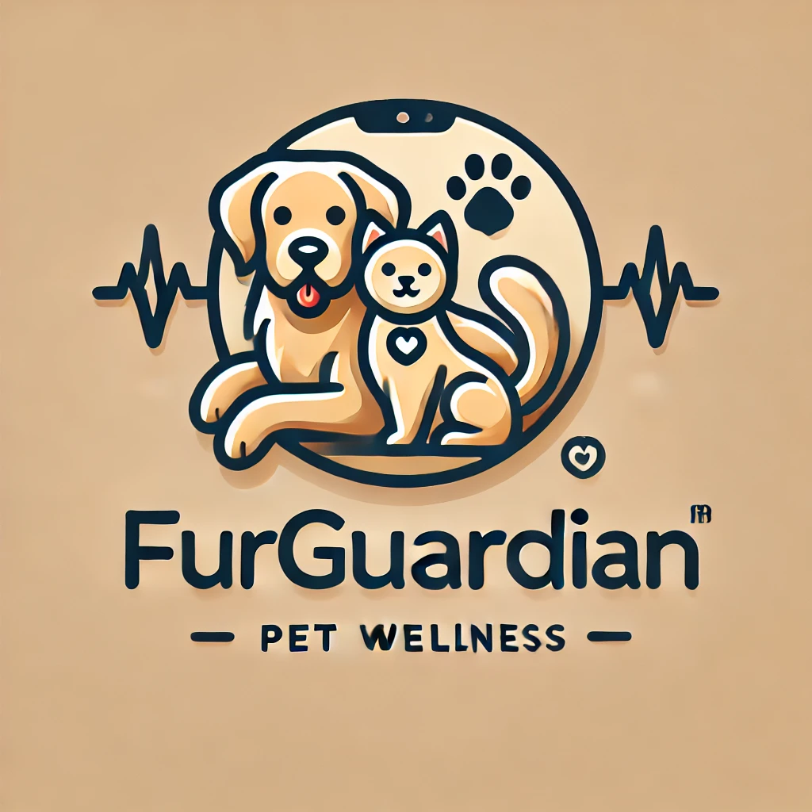
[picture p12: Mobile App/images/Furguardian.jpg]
FurGuardian Logo


### Project Link
[GitHub Repository](https://github.com/Chipman8472/FurGuardian.git)

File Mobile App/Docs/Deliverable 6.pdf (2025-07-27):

# Deliverable 6

Team Name: FurGuardian

Project Name: Pet Wellness App

Team Group: 8

Student Names and ID’s: Justin Chipman – N01598472

Imran Zafurallah - N01585098

Zane Aransevia - N01351168

Tevadi Brookes - N01582563

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
Developers

Name | Student Id | Github Id | Signature | Effort
Justin Chipman | N01598472 | Chipman8472 | Justin C | 100%
Imran Zafurallah | N01585098 | ImranZafurallah5098 | Imran Z | 100%
Zane Aransevia | N01351168 | Zayine917 | Zane A | 100%
Tevadi Brookes | N01582563 | TevadiBrookes2563 | Tevadi B | 100%

Testers

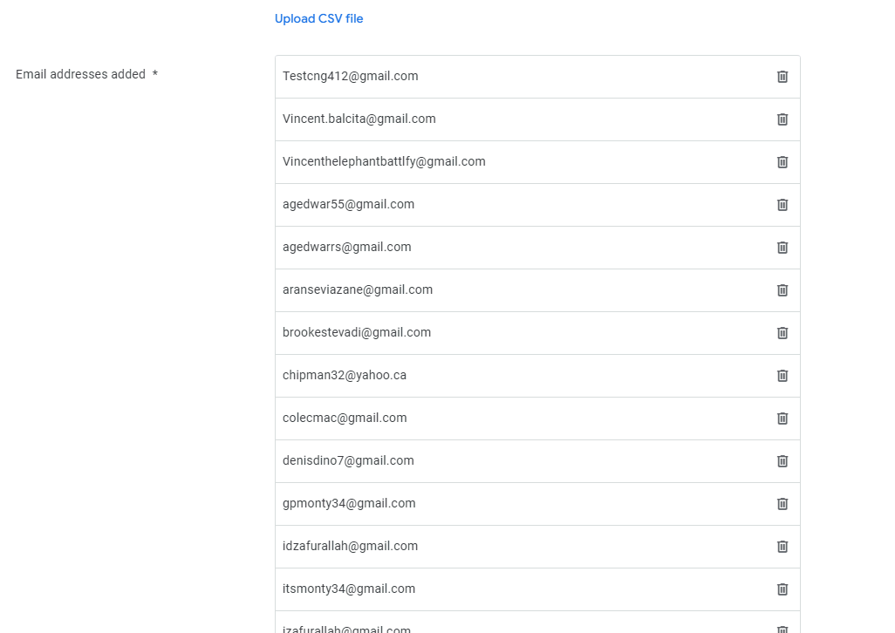
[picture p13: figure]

GitHub Link:

https://github.com/Chipman8472/FurGuardian.git

Upload status and time stamp

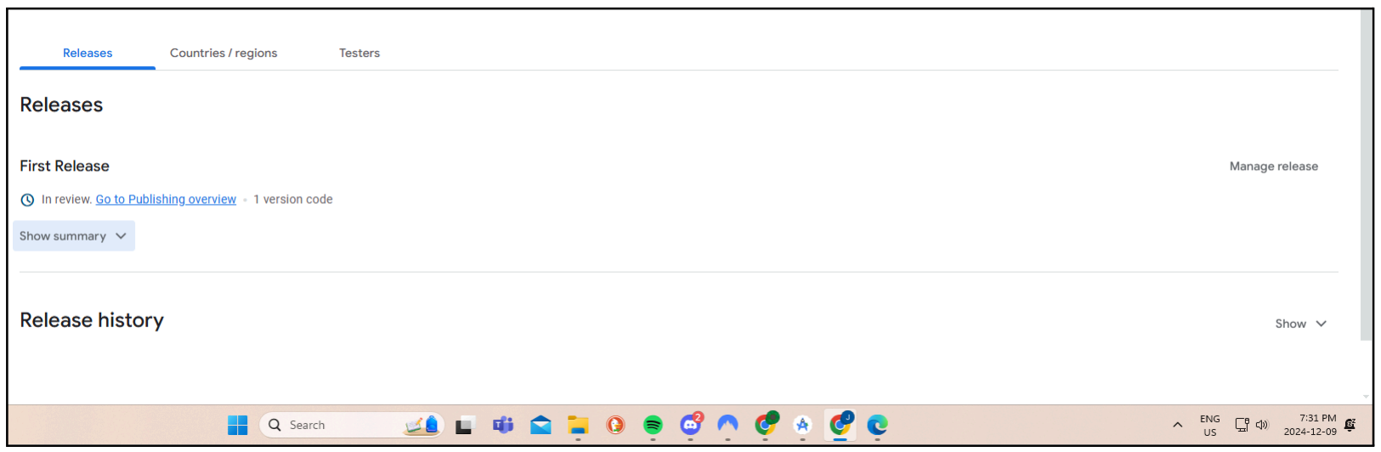
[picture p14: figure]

after approval

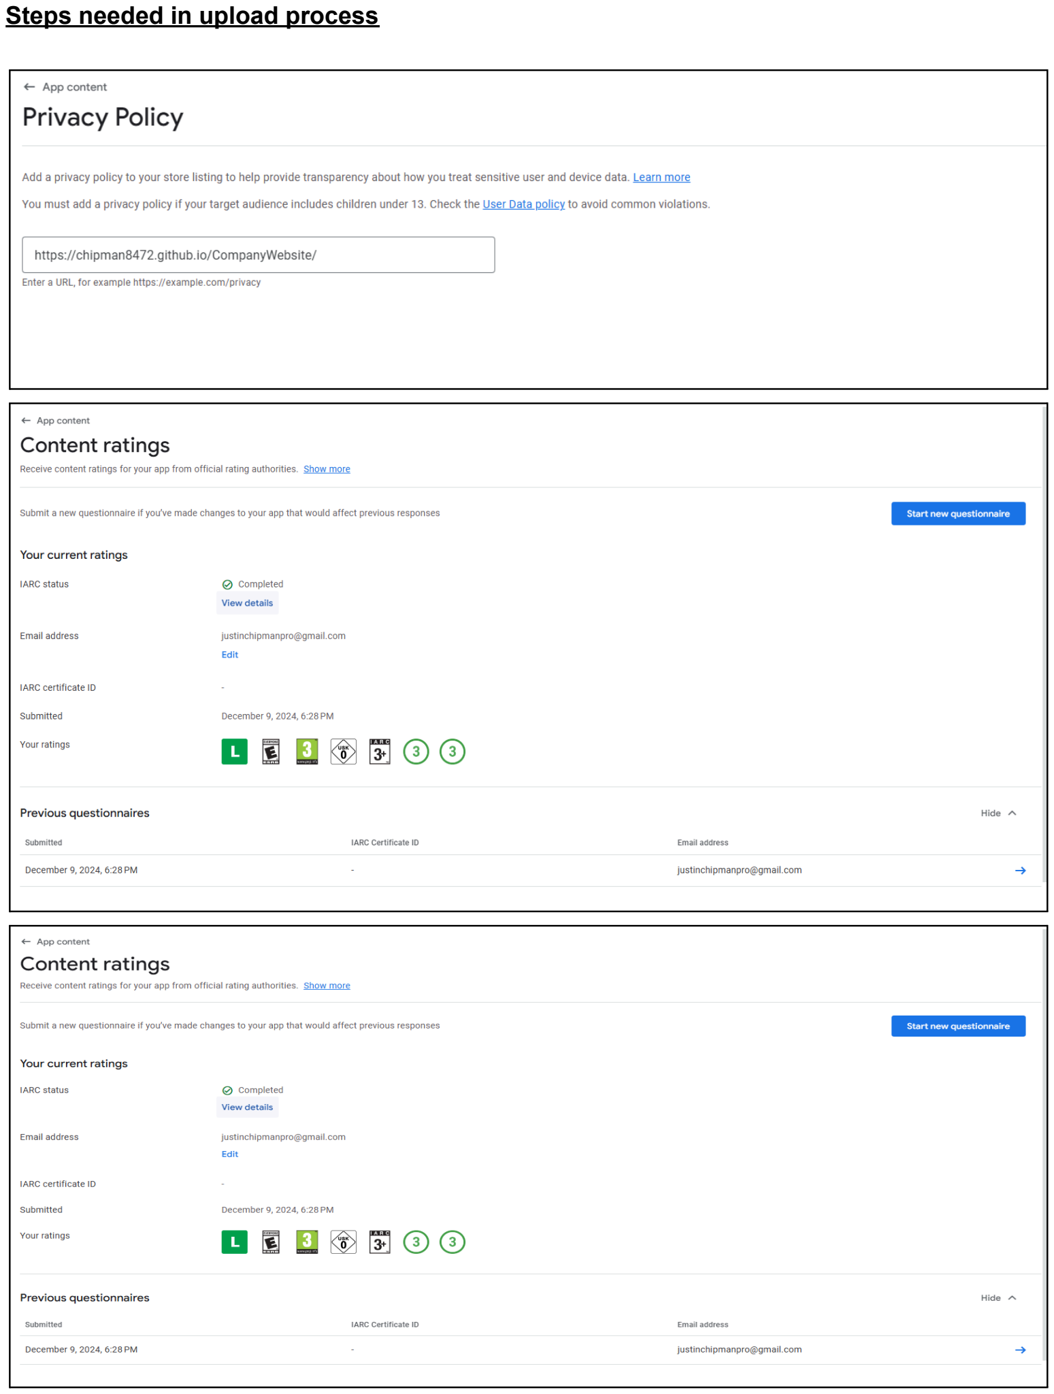
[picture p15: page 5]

Steps needed in upload process

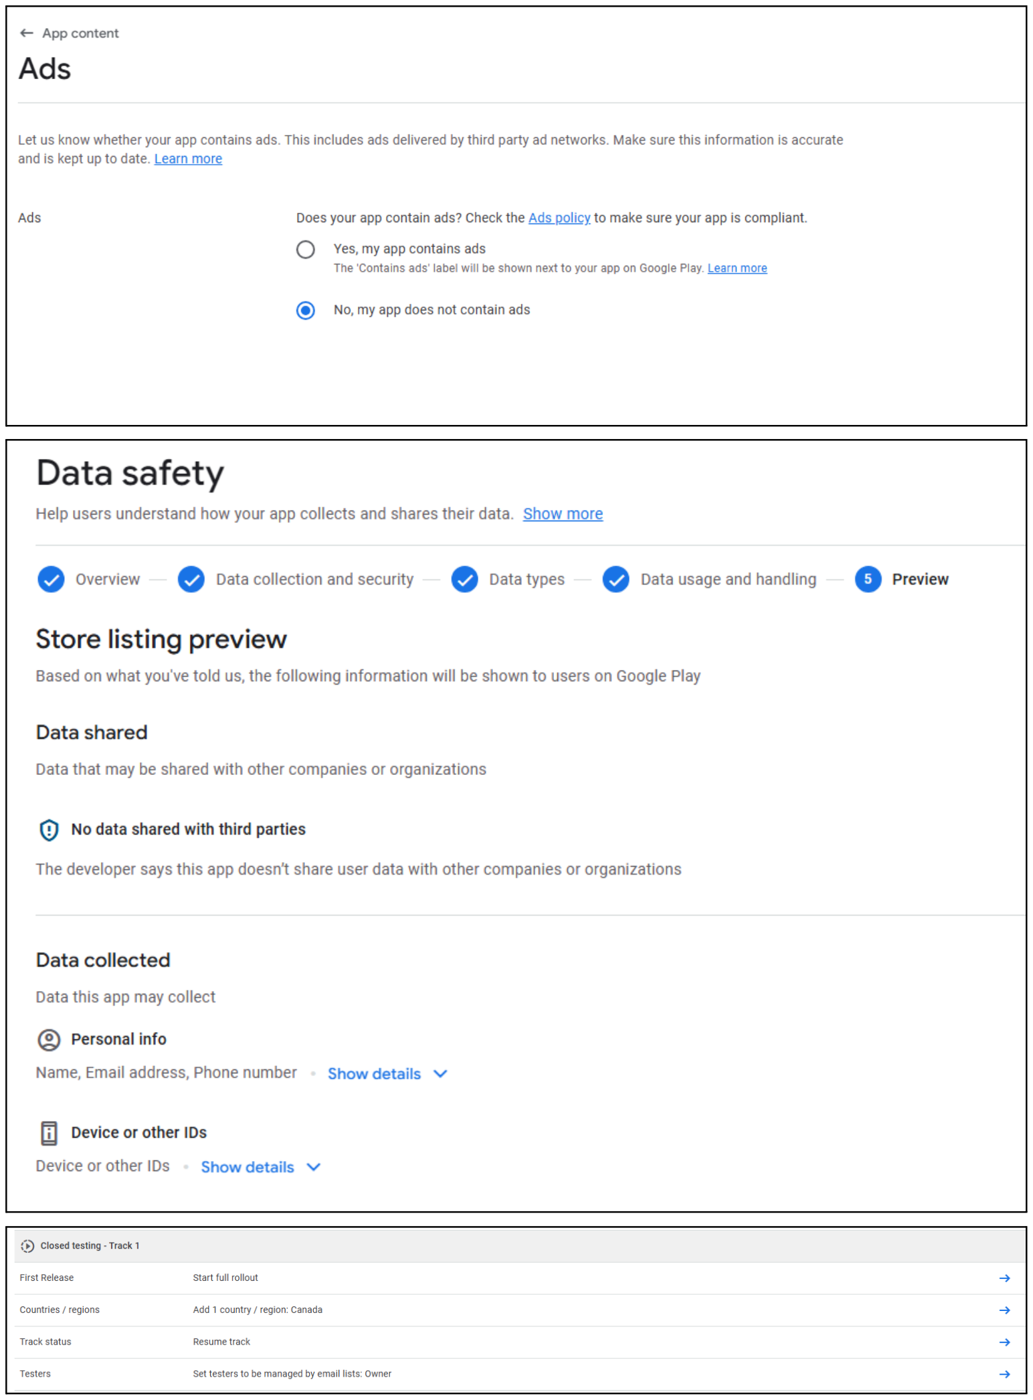
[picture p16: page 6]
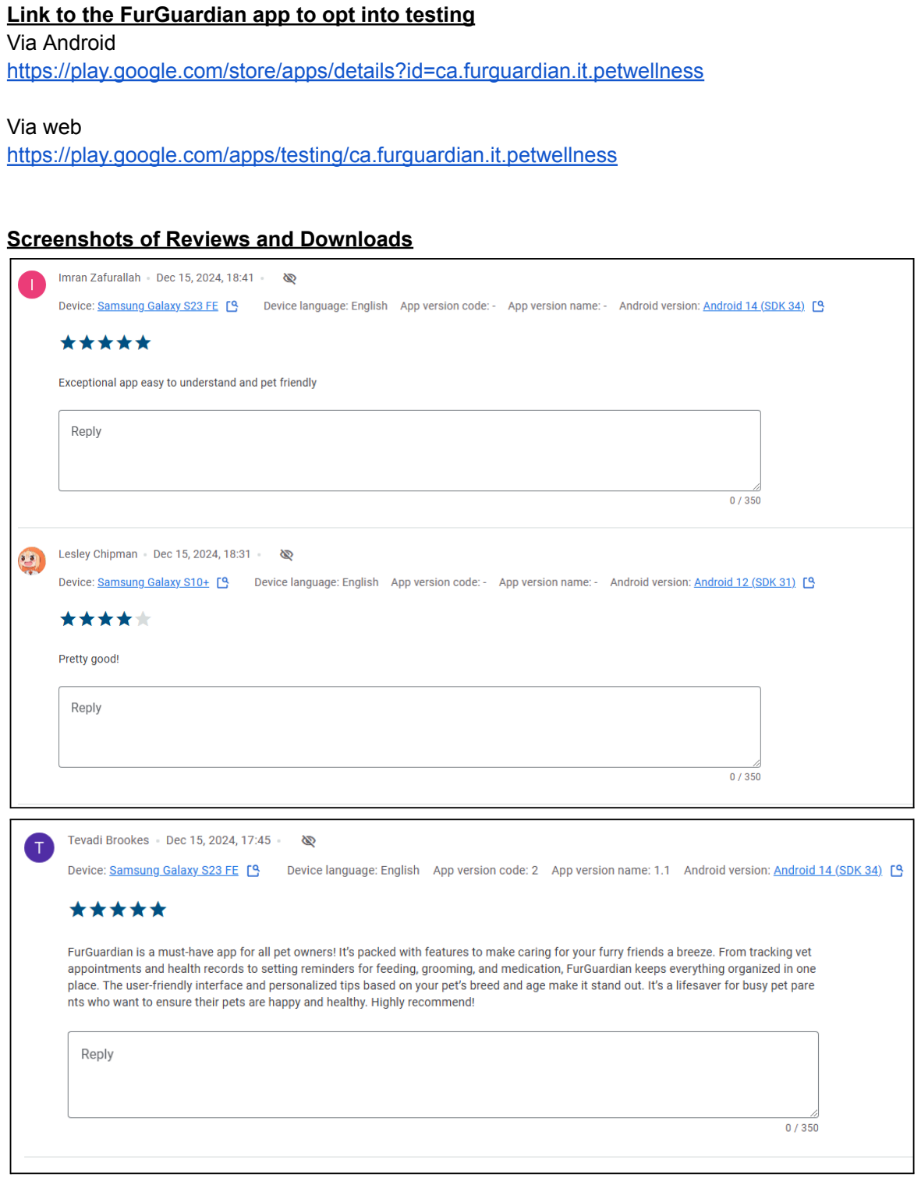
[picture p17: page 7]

Link to the FurGuardian app to opt into testing
Via Android
https://play.google.com/store/apps/details?id=ca.furguardian.it.petwellness

Via web
https://play.google.com/apps/testing/ca.furguardian.it.petwellness

Screenshots of Reviews and Downloads

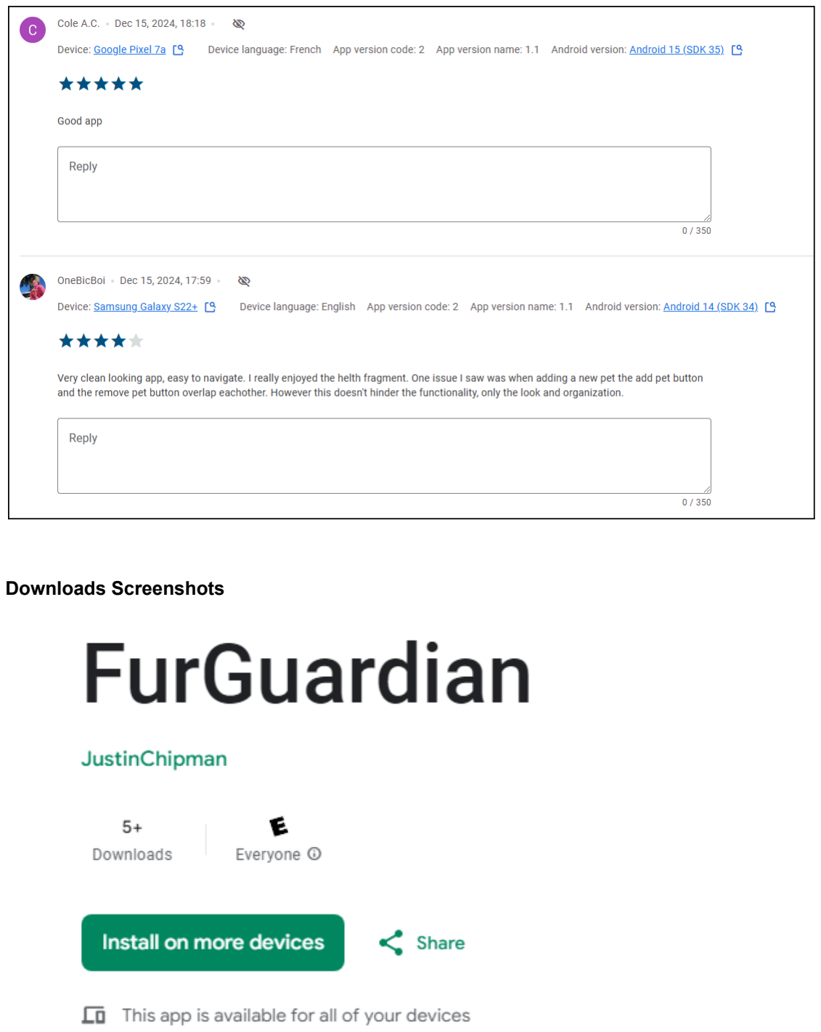
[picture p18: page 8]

Downloads Screenshots

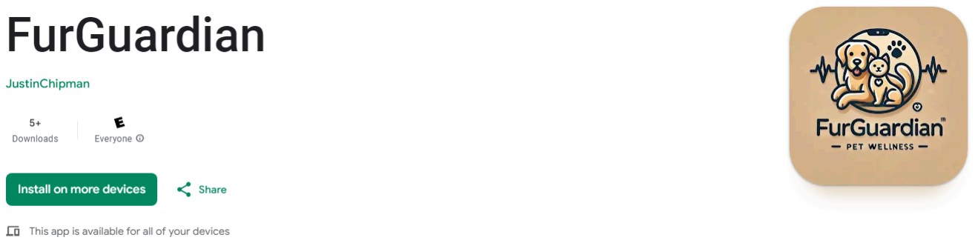
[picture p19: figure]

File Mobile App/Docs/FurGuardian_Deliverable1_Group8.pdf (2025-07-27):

0 | P a g e

# Deliverable 1

Team Name: FurGuardian

Project Name: Pet Wellness App

Team Group: 8

Student Names and ID’s: Justin Chipman – N01598472

Imran Zafurallah - N01585098

Zane Aransevia - N01351168

Tevadi Brookes - N01582563

1 | P a g e

## Contents

## Team Contract

## FurGuardian

[Company Address]
[City, ST ZIP Code]

Please negotiate, sign, scan and include as the first section in your Deliverable 1.

Please note that if cheating is discovered in a group assignment each member will be charged with a cheating offense regardless of their involvement in the offense. Each member will receive the appropriate sanction based on their individual academic honesty history.

Please ensure that you understand the importance of academic honesty. Each member of the group is responsible to ensure the academic integrity of all of the submitted work, not just their own part. Placing your name on a submission indicates that you take responsibility for its content.

2 | P a g e

For further information read Academic Honesty Policy on https://humber.ca/legaland-risk-management/policies/search-by-students.html. (https://humber.ca/legal-and-risk-management/policies/search-by-students.html)

By signing this contract, we acknowledge having read the Humber Academic Honesty Policy as per the link below.

https://academic-regulations.humber.ca/2018-2019/17.0-ACADEMIC-MISCONDUCT

## Responsibilities of the Project Leader include:

- Assigning tasks to other team members, including self, in a fair and equitable manner.
- Ensuring work is completed with accuracy, completeness and timeliness.
- Planning for task completion to ensure timelines are met
- Any other duties as deemed necessary for project completion

What we will do if . . .

Scenario | Accepted initials | We agree to do the following
Team member does not deliver component on time due to severe illness or extreme personal problem | JC TB ZA IZ | a) Team absorbs workload temporarily

Team Member
Names (Please Print)
Signatures | Student ID | Github Id

Project Leader:

Justin Chipman

Justin C | N01598472 | Chipman8472

Zane Aransevia

Zane A | N01351168 | Zayine917

Tevadi Brookes

Tevadi B | N01582563 | TevadiBrookes2563

Imran Zafurallah

Imran Z | N01585098 | ImranZafurallah5098

3 | P a g e
Scenario | Accepted initials | We agree to do the following
Team member cannot deliver component on time due to lack of ability | JC TB ZA IZ | b) Team helps member
Team member does not deliver component on time due to lack of effort | JC TB ZA IZ | b) Team "fires" team member by not permitting his/her name on submission
Team member does not attend team meeting | JC TB ZA IZ | a) Team proceeds without him/her and will assign work to the absent member
An unforeseen constraint occurs after the deliverable has been allocated and scheduled (a surprise test or assignment) | JC TB ZA IZ | a) Team meets and reschedules deliverable
Team cannot achieve consensus leaving one member feeling "railroaded", "ignored", or "frustrated" with a decision which affects all parties | JC TB ZA IZ | a) Team agrees to abide by majority vote

4 | P a g e
Scenario | Accepted initials | We agree to do the following
Team members do not share expectations for grade desired | JC TB ZA IZ | a) Team will elect one person as "standards-bearer" who has the right to ask that work be redone. “Justin Chipman”
Team member behaves in an unprofessional manner by being rude or uncooperative | JC TB ZA IZ | c) Team agrees to avoid use of all vocabulary inappropriate to the business setting
Team member assumes or requests that his/her name be signed to a submission but has not participated in production of the deliverable | JC TB ZA IZ | a) Team agrees that this is cheating and is unethical
There is a dominant team member who is content to make all decisions on the team's behalf leaving some team members feeling like subordinates rather than equal members | JC TB ZA IZ | b) Team will express subordination feelings and attempt to resolve issue
Team has a member who refuses to participate in decision making but complains to others that s/he wasn't consulted | JC TB ZA IZ | c) Team discusses the matter at team meeting

## Project Background and Description

GitHub Link: https://github.com/Chipman8472/FurGuardian.git

5 | P a g e

The goal of FurGuardian is to create a comprehensive pet wellness app that offers pet owners an all-in-one solution for managing their pets’ health, feeding, and activity levels, both in real-time and remotely. The final vision includes an intuitive and feature-rich Android app that provides:

Health monitoring

Medical record management

Remote feeding and monitoring

Wellness alerts

## Software Aspect

The Android app will be developed using Java with Firebase as the backend database for real-time data storage and retrieval. It will interact with various hardware components via Bluetooth or Wi-Fi.

Sensors: Human Detection IR sensor – used to make sure only pets are recognized by the device

DC motor – used to dispense the pet food

RFID sensor – used to detect and differentiate between multiple pets.

Liquid Level Sensor – used to detect if the pets water level is low.

Heart rate sensor – used to detect the pets heart rate.

Scale – to weight food.

Relay – used to dispense treats.

Camera + microphone – for interacting with pets.

## Screen Flow

Our app is designed with a streamlined bottom navigation layout for seamless user interaction. Upon launch, users are greeted by a dynamic splash screen, which transitions into the home screen that streams live video and audio directly from a pet's environment. This feature allows users to monitor and interact with their pets in real-time, fostering a stronger bond even from a distance.

6 | P a g e

The health monitoring screen offers comprehensive insights into your pet’s well-being. Key metrics such as heart rate, hydration, and activity levels are displayed in an intuitive, user-friendly interface, empowering owners to keep their pets in peak condition.

Our feeding schedule feature allows pet owners to remotely manage feeding times and dispense food with just a tap. Users can also monitor water levels, ensuring their pets always have access to fresh water. The medical records screen provides quick access to your pet’s complete medical history, including vaccination schedules and essential health information, ensuring that vital data is always at your fingertips.

Additionally, the insights screen offers valuable educational content about pet care and nutrition, helping users enhance their understanding of pet wellness and make informed decisions.

## Post Interview Feedback Implementation

Feature Expansion: The team added wellness alerts for feeding and health check-ins based on health data, expanding the scope of monitoring.

Improved Usability: Suggestions to enhance the user experience were implemented, such as making the health tracking screen more intuitive and adding easy access to remote feeding controls.

Hardware Integration: Input regarding the RFID sensor for tracking multiple pets and the importance of a water monitoring system was considered to ensure robust functionality.

## Cloud Database READ/WRITE Plan

To satisfy the need for reading and writing data to/from the cloud:

Firebase will be used for real-time data storage. Each pet’s health data (heart rate, hydration, etc.), feeding history, and wellness metrics will be stored in Firebase Firestore.

The app will write pet data (e.g., weight, feeding time, health records) as the sensors collect the data and store it under a unique pet profile in the cloud.

The app will read this data on the owner's device, presenting it in charts and notifications, giving users real-time insights into their pets' wellness.

7 | P a g e

Authentication will be handled using Firebase Authentication to ensure secure access to the data.

Data retrieval will be optimized to support offline functionality in case of network issues, allowing users to view the most recent data until a connection is re-established.

## Project Scope

The technical scope of the FurGuardian project encompasses both the development of the Android app and the integration of hardware components. This involves creating a fully functional and user-friendly application that connects to various hardware sensors, processes pet data, and offers real-time monitoring and interaction.

Week 1-2: Requirements Gathering & Research

Define app features and hardware components.

Research compatible sensors to ensure alignment with project goals.

Week 3-4: UI/UX Design

Create wireframes and mockups.

Plan the user journey for smooth navigation.

Week 5-6: Backend & Database Setup

Set up Firebase Firestore for data storage.

Configure user authentication and cloud access.

Week 7-8: Hardware Integration

Integrate sensors, motor, camera, and microphone with the app.

Test data transmission between hardware and the app.

8 | P a g e

Week 9-10: Core Features Development

Implement health tracking, remote feeding, video monitoring, and notifications.

Ensure real-time data syncing with the cloud.

Week 11-12: Testing & Debugging

Conduct unit and integration testing for the app.

Test hardware operation with the app.

Week 13-14: User Testing & Feedback

Test the app with pet owners.

Refine features and UI based on feedback.

Week 15: Final Deployment

Complete the app for submission to the Google Play Store.

Prepare for the app to go live.

## Integrate Software and Hardware

The FurGuardian app integrates with hardware components like RFID sensors, DC motors, and heart rate sensors using Bluetooth and Wi-Fi for communication. A microcontroller, such as Raspberry Pi or Arduino, serves as the intermediary, collecting data from sensors and sending it to the app, while commands from the app trigger hardware actions, such as dispensing food. This seamless connection ensures that users can manage their pets' wellness remotely, including live video monitoring and health tracking.

The app processes real-time sensor data, such as heart rate or water levels, and displays it for the user, sending alerts when needed. The app-to-hardware communication allows users to interact with pets remotely, with commands like feeding or monitoring live streams being sent to the microcontroller, which triggers hardware responses. Feedback from the hardware is sent back to confirm actions, ensuring reliability and accuracy.

9 | P a g e

To ensure smooth functionality, the team will test hardware components individually, debug communication protocols, and check the app’s real-time data processing. This approach guarantees reliable integration between the app and hardware, providing a comprehensive solution for pet wellness.

## Project Theme Structure

Theme: Develop the "FurGuardian" Pet Health Monitoring & Remote Feeding App

- Epic 1: Heart Rate Monitoring and Activity Tracking
- Story 1: Design and implement heart rate tracking UI
- Task 1: Create UI components for displaying heart rate data in real-time.
- Task 2: Add integration points to receive simulated heart rate data.
- Task 3: Implement logic for refreshing heart rate display at regular intervals.
- Story 2: Develop heart rate data processing logic
- Task 1: Simulate and generate heart rate data.
- Task 2: Implement algorithms to interpret activity levels based on heart rate fluctuations.
- Task 3: Store the data in Firebase for historical tracking.
- Story 3: Create activity insights for pet owners
- Task 1: Analyze stored heart rate data to detect periods of high/low activity.
- Task 2: Provide insights on the pet's activity trends over time (daily, weekly).
- Task 3: Design an insights dashboard for owners to easily view activity levels.
- Epic 2: Food & Hydration Monitoring and Remote Feeding
- Story 1: Create UI for food and hydration tracking
- Task 1: Design food and water level indicators within the app.
- Task 2: Integrate with simulated food dispenser data for real-time tracking.
- Task 3: Implement thresholds to alert owners when food/water levels are low.
- Story 2: Implement food dispenser control (remote/scheduled)
- Task 1: Set up UI controls to allow remote food dispensing.

10 | P a g e
- Task 2: Add logic for scheduling automated feedings.
- Task 3: Simulate food dispensing events and monitor their success in real-time.
- Story 3: Store and retrieve food/hydration data from Firebase
- Task 1: Implement Firebase structure for storing food and hydration data.
- Task 2: Write Java code to sync the dispenser data with Firebase.
- Task 3: Implement retrieval of historical data to show trends over time.
- Epic 3: Health Insights and Medical Records Storage
- Story 1: Create Firebase structure for storing medical records
- Task 1: Design a Firebase schema for holding pet medical records.
- Task 2: Write Java logic to add, update, and delete records in Firebase.
- Task 3: Implement security measures for medical record access (authentication).
- Story 2: Implement health insights algorithm
- Task 1: Create logic to combine heart rate, activity, food, and hydration data into health insights.
- Task 2: Develop algorithms that highlight significant health changes (e.g., dehydration, lethargy).
- Task 3: Display health recommendations and alerts based on insights.
- Story 3: Design health insights UI
- Task 1: Design a user-friendly health insights dashboard.
- Task 2: Integrate real-time and historical health insights into the dashboard.
- Task 3: Allow owners to receive notifications for abnormal health events (e.g., low activity).

## Screenshots

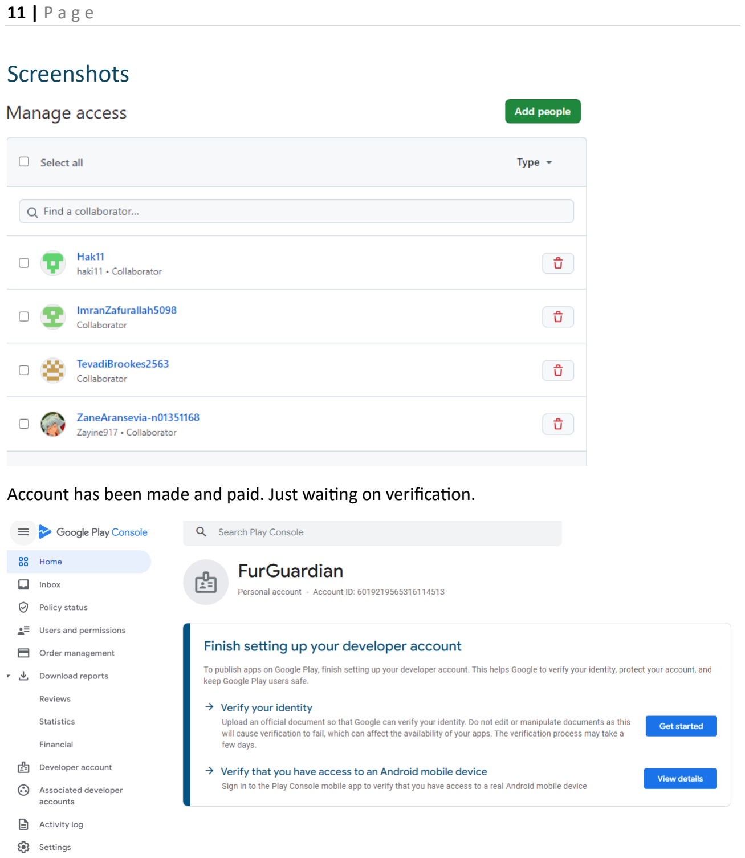
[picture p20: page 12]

11 | P a g e

Account has been made and paid. Just waiting on verification.

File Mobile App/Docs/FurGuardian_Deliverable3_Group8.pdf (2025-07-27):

# Deliverable 3

Team Name: FurGuardian

Project Name: Pet Wellness App

Team Group: 8

Student Names and ID’s:

Justin Chipman – N01598472

Imran Zafurallah - N01585098

Zane Aransevia - N01351168

Tevadi Brookes - N01582563

Name | Student Id | Github Id | Signature | Effort
Justin Chipman | N01598472 | Chipman8472 | Justin C | 100%
Imran Zafurallah | N01585098 | ImranZafurallah5098 | Imran Z | 100%
Zane Aransevia | N01351168 | Zayine917 | Zane A | 100%
Tevadi Brookes | N01582563 | TevadiBrookes2563 | Tevadi B | 100%

Project Scope

The technical scope of the FurGuardian project encompasses both the development of the

Android app and the integration of hardware components. This involves creating a fully

functional and user-friendly application that connects to various hardware sensors, processes pet data, and offers real-time monitoring and interaction.

GitHub Link: https://github.com/Chipman8472/FurGuardian.git

Account Creation in Database

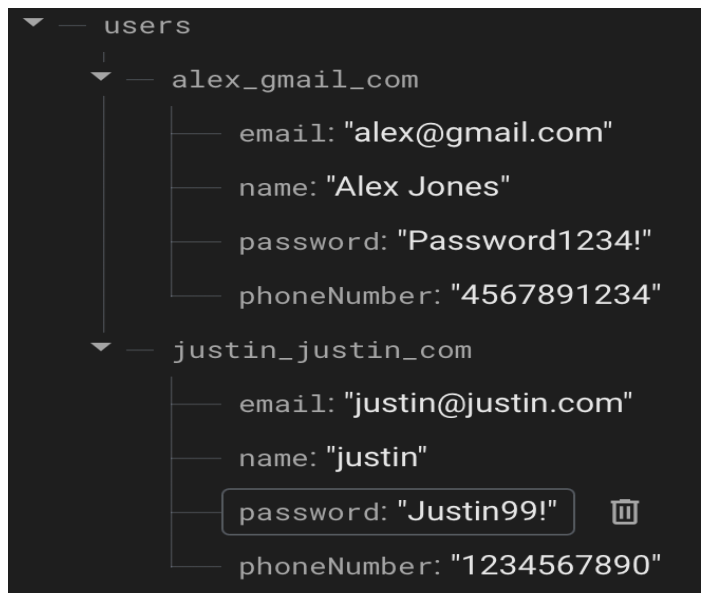
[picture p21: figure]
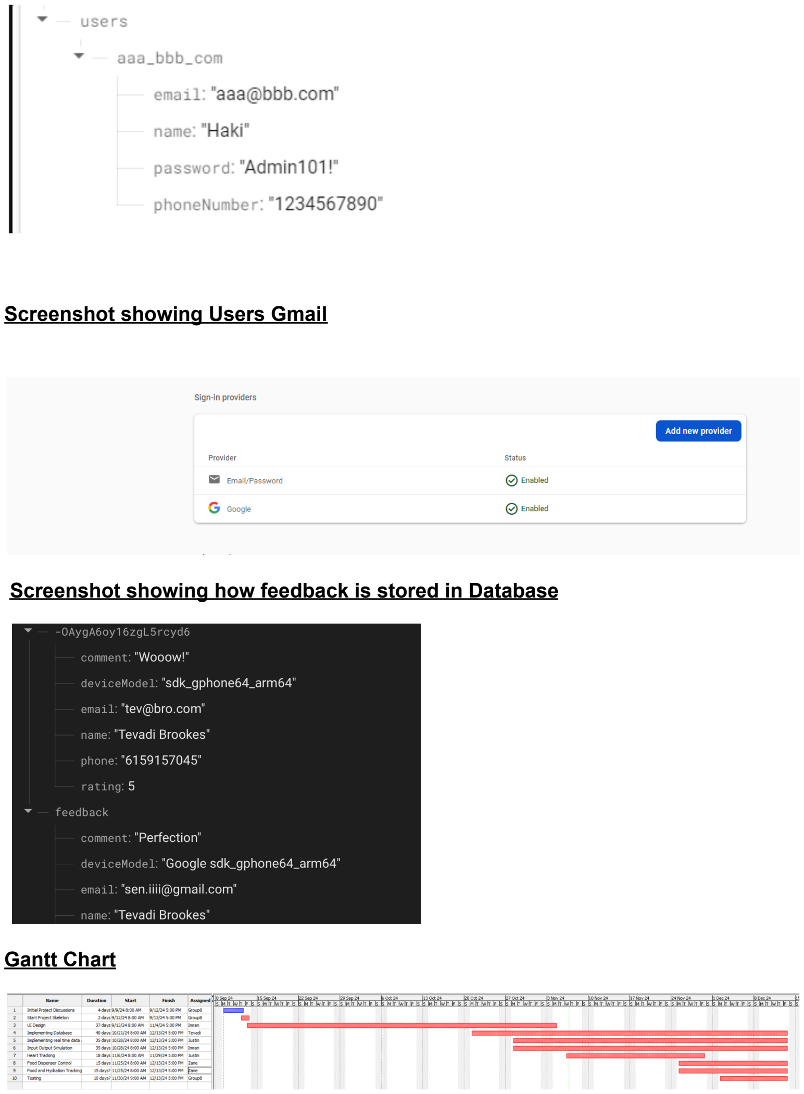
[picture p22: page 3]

Screenshot showing Users Gmail

Screenshot showing how feedback is stored in Database

Gantt Chart

Monday Scrum Board

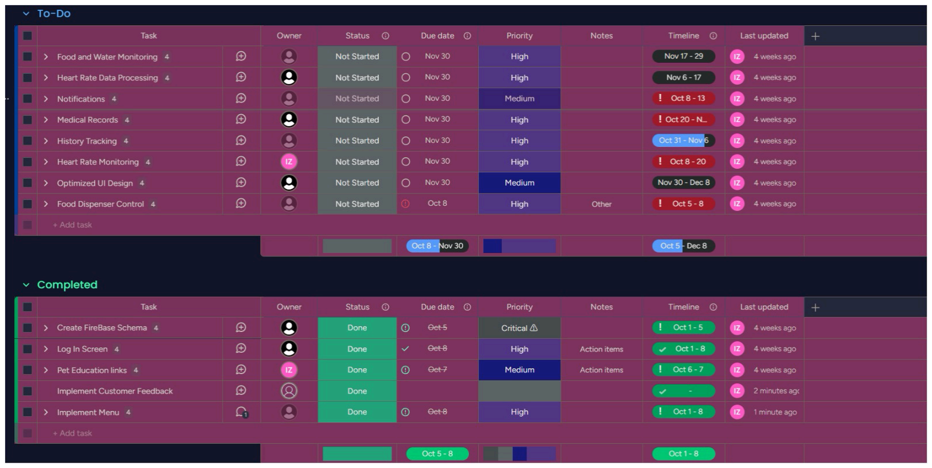
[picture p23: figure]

Sprint 3

Tevadi Brookes for sprint 3 he has developed a Customer Feedback Screen for the app to enable users to submit feedback directly within the app. The design includes input fields for the user’s name, phone number, email, comments, and a RatingBar for satisfaction ratings. Tevadi ensured that all essential fields must be completed before submission, using input validation to improve data quality and user experience. The device model is captured programmatically for backend insights, though it is hidden from the user's view on the screen.

For data handling, he integrated Firebase Realtime Database, with all feedback saved to a dedicated "feedback" collection. This includes the user's personal details, comments, rating, and device model, stored securely for future analysis. The feedback submission process is user-friendly, providing confirmation messages upon successful submissions and error alerts if issues arise. This new feature not only enhances customer engagement within the FurGuardian app but also provides valuable feedback data for continuous improvement of the service.

Justin Chipman developed the Login and Registration System for the app, focused on providing users with a seamless and secure login experience. In addition to traditional account creation, he incorporated Google authentication, allowing users to log in with Gmail without needing a separate account within the app. The login screen also includes a "Remember Me" checkbox, which allows users to stay signed in across sessions without the need to re-enter credentials, while securely managing user sessions without storing sensitive credentials locally on the device. The login screen has also been integrated with a link directing users to the registration screen for easy access.

The Registration Screen ensures secure and validated user data collection, featuring fields for the user’s name, phone number, email, password, and password confirmation. Each input field includes appropriate validation to guarantee data integrity and usability; for example, phone numbers accept only numeric input, and passwords must be confirmed to prevent entry errors. These enhancements provide a robust foundation for user account management, elevating both security and ease of use in the app.

Imran Zafurallah enhanced the Settings and Emergency Contacts features of the app. He implemented functionality for users to add and manage emergency contacts directly within the app, improving the overall safety features for pet owners. Additionally, Imran developed functionality to allow users to update key settings, such as changing the location within the app. This adds flexibility for users for any veterinarians in their proximity, as well as to personalize their experience and ensures the app meets individual preferences.

In addition to these technical improvements, Imran took responsibility for editing and refining the Gantt Chart, ensuring that it accurately reflects large project tasks and milestones. He also updated the Monday dashboard by adding new tasks, marking completed tasks, and ensuring the project’s progress is tracked efficiently. However, to maintain control over task assignments and due to membership limitations, Imran opted to limit the number of individuals with access to the Monday dashboard to just two members. This ensures streamlined communication, with the two members responsible for managing tasks and informing the remaining group members of their duties.

Zane Aransevia worked on enhancing the functionality of the Account Management and pet profile features in his pet wellness app that allows users to view and edit their account details, such as name and phone number, with password change functionality requiring confirmation. He also added a sign-out option and ensured that any updates prompt an "Are you sure?" confirmation to prevent accidental changes.

In addition, Zane developed a system for adding and managing pet profiles within the app. He included features to upload custom images and input the pet's breed and type of animal. Zane ensured that users could easily switch between different pets on the home screen, allowing for a more personalized experience. The pet profiles will persist even after the app is closed, ensuring seamless usage.

Story Breakdowns for Sprint 3

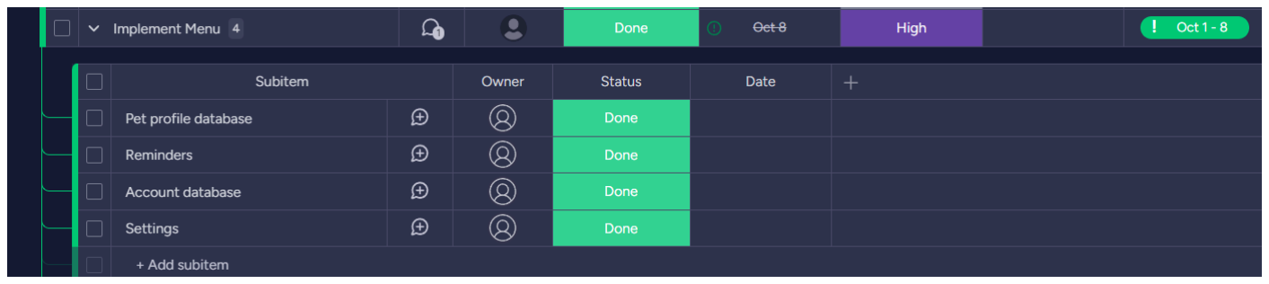
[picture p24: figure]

Daily Standup

Sprint 3

November 3

rd
Justin Chipman | Imran Zafurallah | Zane Aransevia | Tevadi Brookes
What did you do yesterday? | What did you do yesterday? | What did you do yesterday? | What did you do yesterday?
Started developing the login and registration screens, focusing on UI layout and basic field validation. | Went over what I was assigned to do in Sprint 3. | Started designing the health and home screen UI with no implementations. | Work on the initial design to the feedback page
What will you work on today? | What will you work on today? | What will you work on today? | What will you work on today?
Implementation of login and registration screens. | Finished implementing SharedPreferences in the settings screen for Dark Theme preference. | Polish all screen UIs to ensure they meet production standards and address any remaining layout issues for consistency. | Finished implementing SharedPreferences in the settings screen for Dark Theme preference.
Any Blockers? | Any Blockers? | Any Blockers? | Any Blockers?
Not at this time | Not at this time | Not at this time | Not at this time

November 4

th
Justin Chipman | Imran Zafurallah | Zane Aransevia | Tevadi Brookes
What did you do yesterday? | What did you do yesterday? | What did you do yesterday? | What did you do yesterday?
Login and registration screens. | Finished implementing SharedPreferences in the settings screen for Dark Theme preference. | UI designed and fixed previous issues. | Design of the feedback screen.
What will you work on today? | What will you work on today? | What will you work on today? | What will you work on today?
Add Gmail sign-in functionality, implement the “Remember Me” feature, and validate all input fields, especially email and phone number formats. | Begin working on other functionalities in the settings fragment and Emergency Contacts in the top menu. | Implemented writing to Firestore for sensor data and feedback data, including device model information from the feedback screen. | Work on the feedback screen, adding fields for name, phone, email, and comment, along with star rating functionality. Ensure device model is saved to Firestore.
Any Blockers? | Any Blockers? | Any Blockers? | Any Blockers?
Facing some challenges integrating Gmail sign-in and ensuring compatibility across devices. | None to speak of | Not at this time | Not Currently

November 5

th
Justin Chipman | Imran Zafurallah | Zane Aransevia | Tevadi Brookes
What did you do yesterday? | What did you do yesterday? | What did you do yesterday? | What did you do yesterday?
Added Gmail sign-in functionality, implemented the “Remember Me” feature. | Begin working on my task in Settings functionality and Emergency Contacts | Implemented writing to Firestore for sensor data and Pet Profile. | Worked on the functionality of the feedback screen.
What will you work on today? | What will you work on today? | What will you work on today? | What will you work on today?
Complete the runtime permission implementation for accessing device sensors, ensuring permissions are requested when functionality is needed. | Completed settings screen functionality, including saving user-selected themes to SharedPreferences and retaining preferences across sessions. | Finished functionality for Pet profile and health fragment, simulating the proper readings. | Implemented writing to Firestore for feedback data, including device model information from the feedback screen.
Any Blockers? | Any Blockers? | Any Blockers? | Any Blockers?
Some issues with sensor permission handling | Some issues with data being stored in shared pref. | Not Currently | Not at this time

Two different design principles used in the code

Single Responsibility Principle (SRP): Each class has a single responsibility and does not overlap with another class unless to share resources. For instance in our code, the Splash Screen Activity is dedicated solely to managing splash screen functionality such as displaying introductory visuals or initiating app loading procedures without additional logic related to user authentication or other app components. Similarly, the Login Screen is responsible only for user authentication, maintaining clean boundaries between its purpose and other app features.

Don't Repeat Yourself (DRY) Principle: The DRY principle ensures that code is concise, modular, and free of redundancy by promoting reusable methods and components. In FurGuardian, we adhered to the DRY principle by centralizing commonly used features, such as Firebase database interactions and form validation methods. For instance, reusable methods were created for user input validation across the registration and Feedback Screen, minimizing duplicate code and making maintenance more efficient. This approach not only reduces errors but also simplifies future updates, as changes to a single method apply universally across the app.

Open/Closed Principle (OCP) Each class is open for extensions but close for all modifications.

Coding work progress since deliverable 2

Since Deliverable 2, we have made several enhancements to improve the functionality and user experience of the application. A Customer Feedback Screen has been implemented and integrated with Firebase Realtime Database to securely capture and store user feedback. The Login Screen has been enhanced to support Google authentication, allowing Gmail users a seamless login experience. Additionally, an option has been added to enable users to invite others to their account, granting them shared access to pet data.

Further updates include expanded functionality within the Settings Fragment, offering users more control over their app preferences. A Pet Profile feature has also been added, allowing users to manage profiles for multiple pets efficiently. These upgrades collectively enhance the app’s usability, accessibility, and personalization for users managing multiple pets and sharing information with trusted individuals.

Document what runtime permission you have implemented

Runtime permission
private void saveReminder() {
String reminderName = reminderNameEditText.getText().toString();
if (reminderName.isEmpty()) {
Toast.makeText(getContext(), getString(R.string.please_enter_a_reminder_name), Toast.LENGTH_SHORT).show(); return;
}

// Check notification permission
if (Build.VERSION.SDK_INT >= Build.VERSION_CODES.TIRAMISU) {
if (ActivityCompat.checkSelfPermission(requireContext(), Manifest.permission.POST_NOTIFICATIONS) != PackageManager.PERMISSION_GRANTED) { requestNotificationPermission();
return;
}
}

Document the two main functionality of your app that was implemented in this release.


Home Screen Functionality | Pet Profile Functionality

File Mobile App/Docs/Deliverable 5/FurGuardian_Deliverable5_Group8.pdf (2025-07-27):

# Deliverable 5

### Team Name: FurGuardian

### Project Name: Pet Wellness App

### Team Group: 8

### Student Names and ID’s: Justin Chipman – N01598472

### Imran Zafurallah - N01585098

### Zane Aransevia - N01351168

### Tevadi Brookes - N01582563

Name | Student Id | Github Id | Signature | Effort
Justin Chipman | N01598472 | Chipman8472 | Justin C | 100%
Imran Zafurallah | N01585098 | ImranZafurallah5098 | Imran Z | 100%
Zane Aransevia | N01351168 | Zayine917 | Zane A | 100%
Tevadi Brookes | N01582563 | TevadiBrookes2563 | Tevadi B | 100%

### GitHub Link: https://github.com/Chipman8472/FurGuardian.git

Sprint 5 Goals

Tasks from Scrum Dashboard
Describe 3 tasks from the Scrum dashboard that are related to addressing technical debt.

Heart rate processing - update libraries and framework to use stable versions to address know vulnerabilities

Optimized UI Design - create and enhance automated testing for existing functionality to ensure stability.

History Tracking - Update and clean up existing code to improve readability, maintainability, and scalability without changing its external behavior.

The work completed by each member
Justin: I worked on fixing our google sign in as it seems the logic was broken at some point. I updated the database logic by using FirebaseAuth which allowed better storage of our users and increased our security. I implemented our 20 junit tests using both standard methods and robolectrics. I implemented an eye toggle button for the password on our login page to toggle between plain text and "*". As well I just overall worked on fixing imperfections across.

Tevadi: This sprint I added different functionalities that were not there before. I added a snackbar to the reminders fragment, as well as assisted Imran with the clean up of the code. My main focus this sprint was more on the report documentation.

Imran: Worked on cleaning up the java class codes, taking out and adjusting deprecated codes and unused imports for all classes and making sure the app runs with the adjusted codes

Zayine:

C4 Model Component Diagram


Screenshot showing AlertDialog, Snackbar, Toast & Notification




Screenshot of feedback in DB


Screenshots of Data being stored in DB

Screenshot of user data in DB


Screenshot of users

Screenshots of Tests

How Did we address technical debt

One instance of technical debt we faced was when we initially created our database we did not store our database logic correctly in a separate package and class we put it inside of our UI elements directly. On top of that we did not use Authentication right away we simply just stored and retrieved data in plain text.

How we tackled this is by refactoring our code to have different database models such as UserModel in which that class did all the interacting with the database user table. We did that same thing for our data, pet, and feedback table in the database.

Then we upgraded our code to use FirebaseAuth so that we can store users correctly without using plain text and also incorporate other sign in methods such as Google Sign in.

Refactored Code

Before refactoring our health data simulation code the health markers were completely random. After refactoring we decided to make the values represent more realistic values. So we refactored the code to mimic more real life scenarios. The code has been commented to show how it represents real life examples

After Refactor
// Method to simulate more realistic health data
public Map<String, Object> simulateData() {
// Heart rate (bpm): Normal resting heart rate is between 60 and 100 int heartRate = generateHeartRate();

// Respiratory rate (breaths per minute): Normal is between 12 and 20
int respiratoryRate = generateRespiratoryRate();

// Steps: Average steps per day can range between 4000 and 12000, depending on activity
int steps = generateStepCount();

// Distance (km): Daily distance walked based on steps, average stride length is 0.762 meters
double distance = steps * 0.000762; // Convert steps to km (0.762m per step)

// Sleep hours: 7-9 hours, but it can vary slightly for shorter or longer sleepers
double sleepHours = generateSleepHours();

// Weight (kg): Slight fluctuations based on meals, hydration, and activity double weight = generateWeight();

// Prepare the data map to store in Firebase Map<String, Object> data = new HashMap<>(); data.put("heartRate", heartRate); data.put("respiratoryRate", respiratoryRate); data.put("steps", steps);
data.put("distance", distance); data.put("sleepHours", sleepHours); data.put("weight", weight);

return data;
}

// Simulates realistic heart rate private int generateHeartRate() { double activityFactor = Math.random();
if (activityFactor < 0.2) { // Resting
return 60 + random.nextInt(10); // 60-69 bpm
} else if (activityFactor < 0.7) { // Light activity return 70 + random.nextInt(20); // 70-89 bpm
} else { // High activity
return 90 + random.nextInt(20); // 90-109 bpm }
}

// Simulates realistic respiratory rate private int generateRespiratoryRate() { double activityFactor = Math.random();
if (activityFactor < 0.3) { // Resting
return 12 + random.nextInt(3); // 12-14 breaths/min } else if (activityFactor < 0.8) { // Light activity return 15 + random.nextInt(4); // 15-18 breaths/min } else { // High activity
return 19 + random.nextInt(2); // 19-20 breaths/min }
}

// Simulates realistic step count
private int generateStepCount() {
double activityLevel = Math.random();
if (activityLevel < 0.3) { // Sedentary day
return 2000 + random.nextInt(2000); // 2000-3999 steps } else if (activityLevel < 0.7) { // Moderately active day return 4000 + random.nextInt(4000); // 4000-7999 steps } else { // Very active day
return 8000 + random.nextInt(5000); // 8000-12999 steps }
}

// Simulates realistic sleep hours private double generateSleepHours() { double sleepQuality = Math.random();
if (sleepQuality < 0.3) { // Poor sleep
return 5 + random.nextDouble(); // 5-6 hours
} else if (sleepQuality < 0.7) { // Average sleep return 7 + random.nextDouble() * 2; // 7-9 hours } else { // Good sleep
return 9 + random.nextDouble(); // 9-10 hours }
}

// Simulates realistic weight fluctuations
private double generateWeight() {
double baselineWeight = 7.0; // Assuming 7.0kg as average for the subject return baselineWeight + (random.nextDouble() * 0.3 - 0.15); // +/- 0.15kg fluctuation
}

Another example of how we refactored our code is with the Registration activity. Before we refactored it we had all the input validation inside the UI class and we also had all the database logic in there as well. After refactoring it the code became a simple if-else statement with all the rest of the logic being handled by the InputValidator class and the UserModel class.

After refactor
// InputValidator now handles all the logic for input validation making the code much cleaner. if (!InputValidator.isValidEmail(email)) {
Toast.makeText(this, getString(R.string.invalid_email_format), Toast.LENGTH_SHORT).show();
} else if (!InputValidator.isValidPhoneNumber(phone)) { Toast.makeText(this, getString(R.string.phone_number_must_be_10_digits), Toast.LENGTH_SHORT).show();
} else if (!InputValidator.isValidPassword(password)) {
Toast.makeText(this,
getString(R.string.password_must_be_8_16_characters_contain_at_least_1_upperca se_letter_1_number_and_1_symbol), Toast.LENGTH_LONG).show();
} else if (!password.equals(confirmPassword)) {
Toast.makeText(this, getString(R.string.passwords_do_not_match1), Toast.LENGTH_SHORT).show();
} else {
SharedPreferences sharedPreferences = getSharedPreferences("userPrefs", Context.MODE_PRIVATE);
SharedPreferences.Editor editor = sharedPreferences.edit(); editor.putString(getString(R.string.email), email); editor.putString(getString(R.string.password1), password); editor.apply();

// User Model now handles the Database logic we simply just pass the information gathered by the UI elements. userModel.registerUser(email, password, name, phone, this, new UserModel.RegistrationCallback() {
@Override
public void onRegistrationSuccess() { Toast.makeText(RegistrationActivity.this, getString(R.string.registration_successful1), Toast.LENGTH_SHORT).show(); startActivity(new Intent(RegistrationActivity.this, MainActivity.class));
finish();
}

@Override
public void onRegistrationFailed(String errorMessage) { Toast.makeText(RegistrationActivity.this, errorMessage, Toast.LENGTH_LONG).show(); }
});
}

below is a look at our registerUser method in UserModel

// Register a new user
public void registerUser(String email, String password, String name, String phoneNumber, Context context, RegistrationCallback callback) { auth.createUserWithEmailAndPassword(email, password).addOnCompleteListener(task -> {
if (task.isSuccessful()) {
FirebaseUser firebaseUser = auth.getCurrentUser(); if (firebaseUser != null) {
String userId = firebaseUser.getUid();

// Store user details in Realtime Database
User newUser = new User(email, name, phoneNumber);

usersRef.child(userId).setValue(newUser).addOnCompleteListener(dbTask -> { if (dbTask.isSuccessful()) { callback.onRegistrationSuccess(); } else {

callback.onRegistrationFailed(context.getString(R.string.failed_to_save_user_da ta));
}
});
}
} else {

callback.onRegistrationFailed(task.getException().getMessage()); }
});
}

Below is a look at our InputValidator class

// Validates if the email is in a valid format
public static boolean isValidEmail(String email) {
if (email == null) return false;
String emailRegex = "^[a-zA-Z0-9._%+-]+@[a-zA-Z0-9.-]+\\.[a-zA-Z]{2,6}$"; return email.matches(emailRegex);
}

// Validates if the phone number is exactly 10 digits (for North American numbers)
public static boolean isValidPhoneNumber(String phoneNumber) {
return phoneNumber != null && phoneNumber.matches("\\d{10}");
}

// Validates if the password meets the required criteria
public static boolean isValidPassword(String password) {
if (password == null || password.length() < 8 || password.length() > 16) { return false;
}

Pattern pattern =
Pattern.compile("^(?=.*[A-Z])(?=.*[0-9])(?=.*[!@#$%^&*+=]).{8,16}$"); Matcher matcher = pattern.matcher(password);

return matcher.matches();
}

Describe how DevOps would have helped your project

Streamlined Development and Deployment- by Continuous Integration/Continuous Deployment (CI/CD) pipelines automating building, testing, and deploying code, ensuring rapid delivery of new features and updates.

Reduced Technical Debt-having regular refactoring and maintenance as part of automated pipelines and collaborative workflows will reduce the technical debt significantly.

Risk Mitigation- Incremental changes, automated testing, and rollback mechanisms reduce the risk associated with deploying updates.

Security Vulnerability

The security vulnerability here is that we are storing the users email and phone number in plain text. This is an issue because if there is a data breach this information will be leaked and the users could receive an increase in spam or robo calls. Potentially make them more susceptible to phishing attempts.

How we would change this in the future is by using encryption to store this data so that even if there is a breach the data will be unreadable.

Security threat Code
public void submitFeedback(String name, String phone, String email, String comment, float rating, Context context, FeedbackCallback callback) {
// Prepare feedback data
String deviceModel = android.os.Build.MODEL;
Map<String, Object> feedback = new HashMap<>(); feedback.put("name", name); feedback.put("phone", phone); feedback.put("email", email); feedback.put("comment", comment); feedback.put("rating", rating); feedback.put("deviceModel", deviceModel);

// Add feedback data to Firebase feedbackRef.push().setValue(feedback) .addOnSuccessListener(aVoid -> {
// Notify success through callback if (callback != null) {
callback.onSuccess();
}
})
.addOnFailureListener(e -> {
// Notify failure through callback
if (callback != null) {
callback.onFailure(e.getMessage()); }
});
}

Project Review Meeting (names of who attended written on the sticky notes)


Monday


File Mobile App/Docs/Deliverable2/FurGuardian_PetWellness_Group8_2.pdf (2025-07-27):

# Deliverable 2

Team Name: FurGuardian
Project Name: Pet Wellness App Team Group: 8
Student Names and ID’s: Jusn Chipman – N01598472 Imran Zafurallah - N01585098 Zane Aransevia - N01351168 Tevadi Brookes - N01582563

## Contents

Name | Student Id | Github Id | Signature | Effort
Jusn Chipman | N01598472 | Chipman8472 | Jusn C | 100%
Imran Zafurallah | N01585098 | ImranZafurallah5098 | Imran Z | 100%
Zane Aransevia | N01351168 | Zayine917 | Zane A | 75%
Tevadi Brookes | N01582563 | TevadiBrookes2563 | Tevadi B | 100%

## Project Scope

The technical scope of the FurGuardian project encompasses both the development of the Android app and the integraon of hardware components. This involves creang a fully funconal and user-friendly applicaon that connects to various hardware sensors, processes pet data, and offers real-me monitoring and interacon.

Week 1-2: Requirements Gathering & Research
Define app features and hardware components.
Research compable sensors to ensure alignment with project goals.

Week 3-4: UI/UX Design
Create wireframes and mockups.
Plan the user journey for smooth navigaon.

Week 5-6: Backend & Database Setup
Set up Firebase Firestore for data storage. Configure user authencaon and cloud access.

Week 7-8: Hardware Integraon
Integrate sensors, motor, camera, and microphone with the app.
Test data transmission between hardware and the app.
Week 9-10: Core Features Development
Implement health tracking, remote feeding, video monitoring, and noficaons. Ensure real-me data syncing with the cloud.

Week 11-12: Tesng & Debugging
Conduct unit and integraon tesng for the app. Test hardware operaon with the app.

Week 13-14: User Tesng & Feedback
Test the app with pet owners.
Refine features and UI based on feedback.

Week 15: Final Deployment
Complete the app for submission to the Google Play Store. Prepare for the app to go live.

## Github Strategy and link

Our GitHub strategy has been for everyone to work on separate features on different branches and then when the feature is complete we merge our codes into the master branch while discussing the merge conflicons with each other to ensure the merge is done correctly. htps://github.com/Chipman8472/FurGuardian.git

## Agile Breakdown

### Theme: Develop the "FurGuardian" Pet Health Monitoring & Remote Feeding App

- Epic 1: Heart Rate Monitoring and Acvity Tracking
- Story 1: Design and implement heart rate tracking UI
- Task 1: Create UI components for displaying heart rate data in real-me.
- Task 2: Add integraon points to receive simulated heart rate data.
- Task 3: Implement logic for refreshing heart rate display at regular intervals.
- Task 4: Opmize UI layout for different screen sizes and orientaons.
- Story 2: Develop heart rate data processing logic
- Task 1: Simulate and generate heart rate data.
- Task 2: Implement algorithms to interpret acvity levels based on heart rate fluctuaons.
- Task 3: Store the data in Firebase for historical tracking.
- Task 4: Implement error-handling and validaon to ensure data accuracy and prevent outliers.
- Story 3: Create acvity insights for pet owners
- Task 1: Analyze stored heart rate data to detect periods of high/low acvity.
- Task 2: Provide insights on the pet's acvity trends over me (daily, weekly).
- Task 3: Design an insights dashboard for owners to easily view acvity levels.
- Task 4: Implement a "download report" feature that exports acvity insights as a PDF.
- Epic 2: Food & Hydraon Monitoring and Remote Feeding
- Story 1: Create UI for food and hydraon tracking
- Task 1: Design food and water level indicators within the app.
- Task 2: Integrate with simulated food dispenser data for real-me tracking.
- Task 3: Implement thresholds to alert owners when food/water levels are low.

- Task 4: Design push noficaons to alert users when thresholds are reached.
- Story 2: Implement food dispenser control (remote/scheduled)
- Task 1: Set up UI controls to allow remote food dispensing.
- Task 2: Add logic for scheduling automated feedings.
- Task 3: Simulate food dispensing events and monitor their success in real-me.
- Task 4: Implement a failsafe to handle scheduled feedings if the app is offline or the network connecon fails.
- Story 3: Store and retrieve food/hydraon data from Firebase
- Task 1: Implement Firebase structure for storing food and hydraon data.
- Task 2: Write Java code to sync the dispenser data with Firebase.
- Task 3: Implement retrieval of historical data to show trends over me.
- Task 4: Add filtering and sorng opons for the food and hydraon data (e.g., by date, quanty).
- Epic 3: Health Insights and Medical Records Storage
- Story 1: Create Firebase structure for storing medical records
- Task 1: Design a Firebase schema for holding pet medical records.
- Task 2: Write Java logic to add, update, and delete records in Firebase.
- Task 3: Implement security measures for medical record access (authencaon).
- Task 4: Set up backup and recovery opons for medical records in case of data corrupon.
- Story 2: Implement health insights algorithm
- Task 1: Create logic to combine heart rate, acvity, food, and hydraon data into health insights.
- Task 2: Develop algorithms that highlight significant health changes (e.g., dehydraon, lethargy).
- Task 3: Display health recommendaons and alerts based on insights.
- Task 4: Integrate machine learning to improve the accuracy of health insights and recommendaons over me.
- Story 3: Design health insights UI
- Task 1: Design a user-friendly health insights dashboard.

- Task 2: Integrate real-me and historical health insights into the dashboard.
- Task 3: Allow owners to receive noficaons for abnormal health events (e.g., low acvity).
- Task 4: Implement a customizable noficaon system allowing owners to set their own alert thresholds for specific metrics.

## Charts and Screenshots

Menu

Gant Chart


Firebase Database


We are in the process of securely fetching and managing account informaon, ensuring efficient and reliable data handling. Our plaorm is designed to store and retrieve medical records


seamlessly, providing easy access to crical health data. Addionally, we integrate data from hardware components and sensors to offer comprehensive real-me monitoring and insights. Monday.com Tasks
Overview

Breakdown


Hardware professor invite:

## List of DoD

Firebase Implementaon
Login screen implementaon Pet Educaon Fragment

Explanaon:
We met the DoD by thoroughly tesng the different login and data fetching cases. Inially we had issues with the app crashing if the user info was not found in the database or if the user input didn’t match the corresponding data type. By adding in sufficient input validaon we solved this problem. The tesng for pet educaon fragment was much less extensive as the links worked under any circumstance, however we need to look into keeping the links up to date and possibly automang this.

## Daily stand-ups outcome

Date | Team Member | Update/Task | Notes
03-10-2024 | Team Discussion | Ensured connuity of color and theme throughout the app. | Final color palete needs approval.
04-10-2024 | Team Discussion | Specified menu items with intuive labels and clear navigaon. | Mock-up menu design is ready.
06-10-2024 | Team Discussion | Finalized list of required images for app, including icons and illustraons. | N/A
08-10-2024 | Jusn Chipman | Firebase schema for login screen completed. | Security features in progress.
07-10-2024 | Zane Aransevia | Menu Items/Bar | Funconality required.
07-10-2024 | Imran Zafurallah | Pet Educaon Links to be implemented. | Working on Calendar event creaon.
08-10-2024 | Tevadi Brookes | Seng Screen | Funconality needs improvement.

## Business Model Canvas

1. Customer Segments
- Pet product retailers (PetSmart, etc...)
- Veterinarians
- Pet owners

2. Value Proposion
- Providing real-me pet health monitoring and remote feeding opons to ensure pet well-being for owners.
3. Channels
- Mobile app (Play Store, App Store)
- Social Media
- Veterinarians
4. Customer Relaonships
- 24/7 customer support
- Community engagement (forums, etc...)
- Personalized noficaons
5. Revenue Streams
- Subscripon fees
- In-app purchases
- Hardware sales
6. Key Acvies
- App Development
- Markeng
- Customer support
7. Key Resources
- Developers
- Cloud infrastructure
- Partnerships with veterinarians

8. Key Partnerships
- Form partnerships with veterinarians or clinics for insights into pet health data and recommendaons
- Partner with pet product suppliers
- IoT devices manufacturers that specialize in producing pet health monitors or automated feeders.
9. Cost Structure
- Adversement
- Markeng and customer support
- App development and maintenance

## Coding Progress Since Deliverable 1

- Implemented login screen + registraon
- Implemented database to store user details
- Implemented the educaon fragment with links to different educaonal resources
- Implemented a reminder menu opon with push noficaons + permissions requests
- Developed a theme for the app
- Created the sengs menu

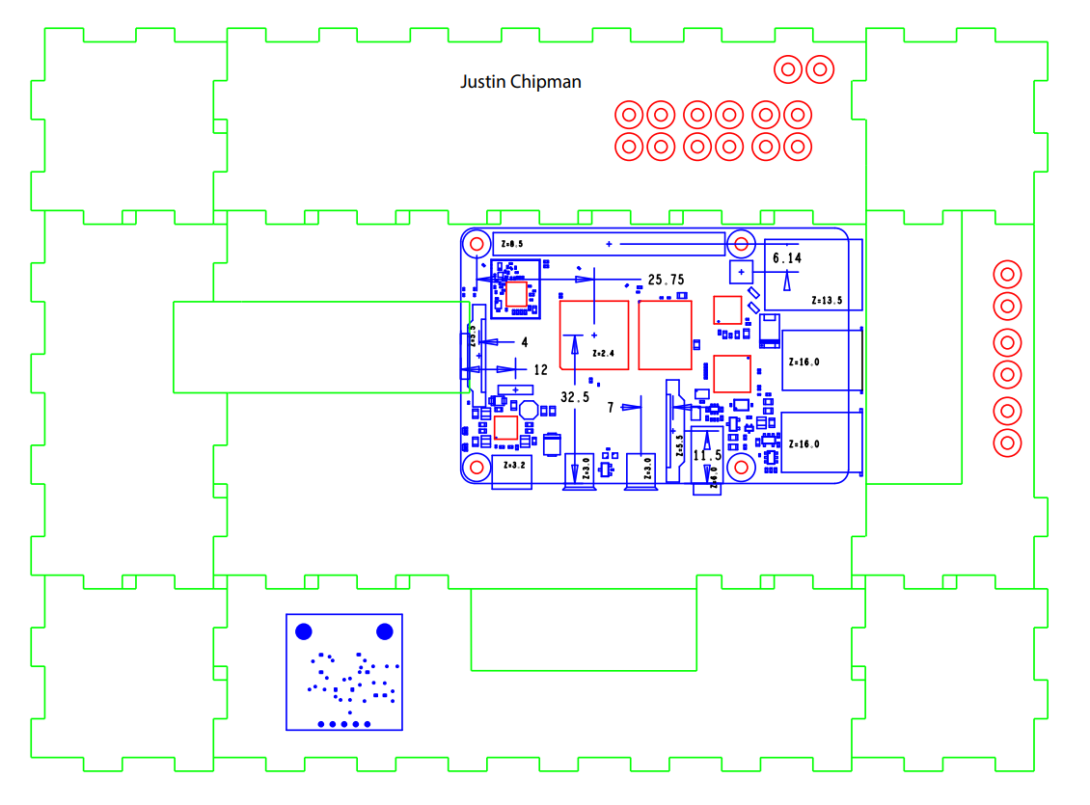
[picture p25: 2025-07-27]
hardware/lasercutting/Case-design.png

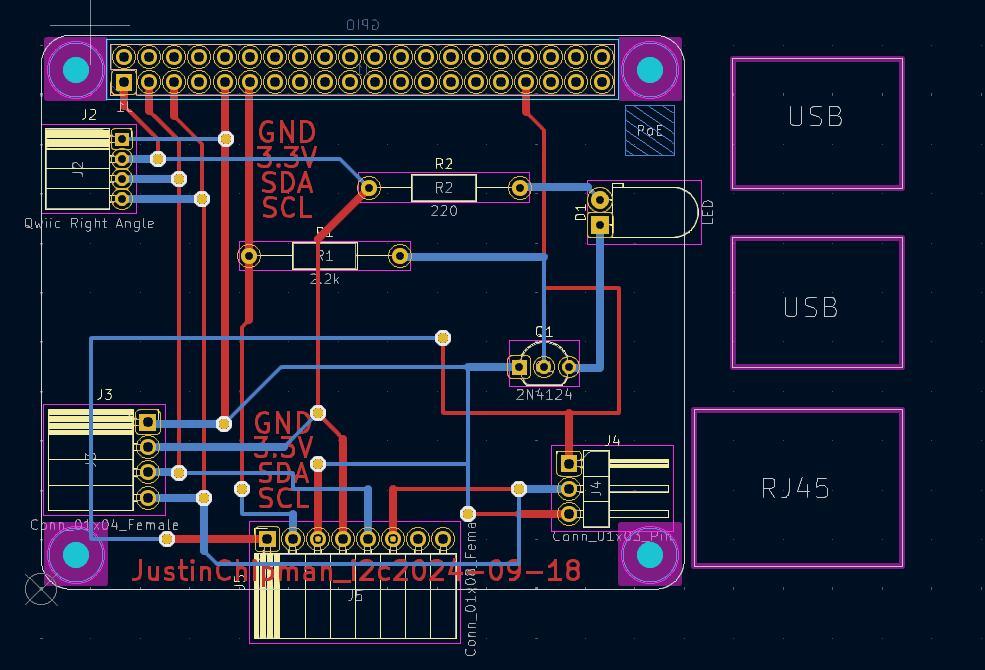
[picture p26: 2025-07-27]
hardware/pcb/PCB_design.png

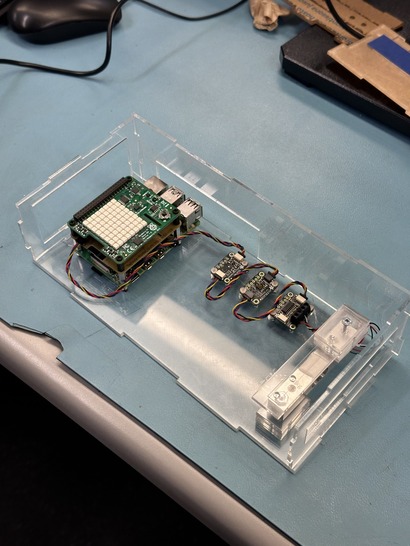
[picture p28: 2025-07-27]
hardware/lasercutting/StudiousCase.jpg

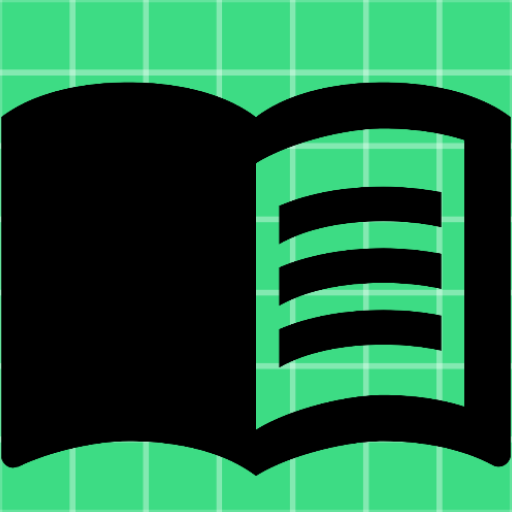
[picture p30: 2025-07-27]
Mobile App/FurGuardian/src/main/ic_records-playstore.png

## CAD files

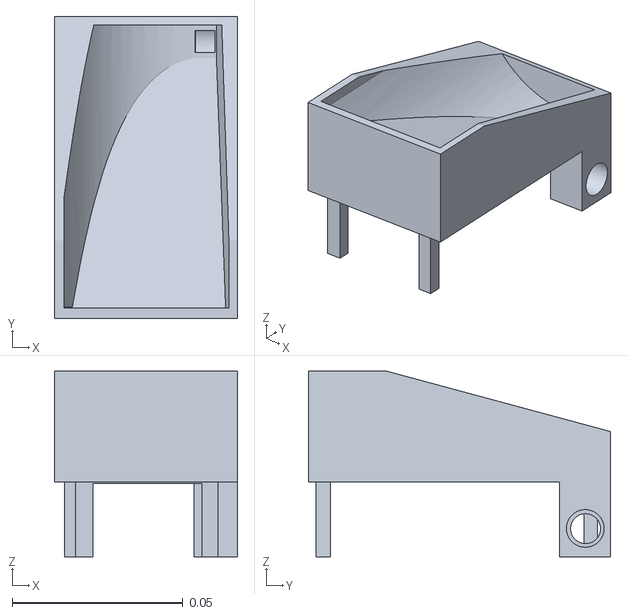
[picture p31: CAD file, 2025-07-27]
hardware/3dprinting/Resevoir.stl
0.0536 x 0.0884 x 0.0544

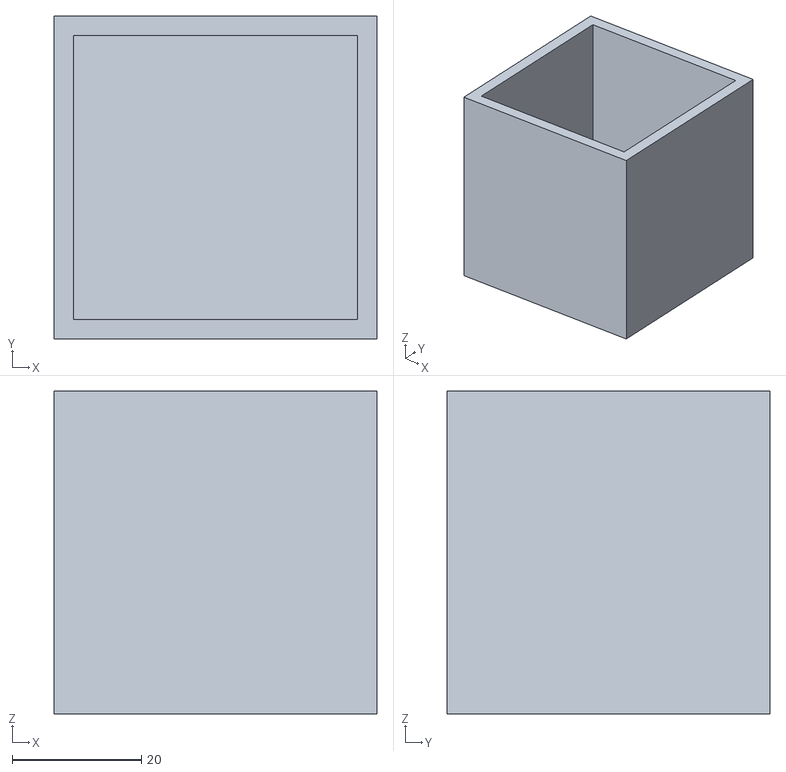
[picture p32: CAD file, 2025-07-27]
hardware/3dprinting/openbox.stl
50.0 x 50.0 x 50.0

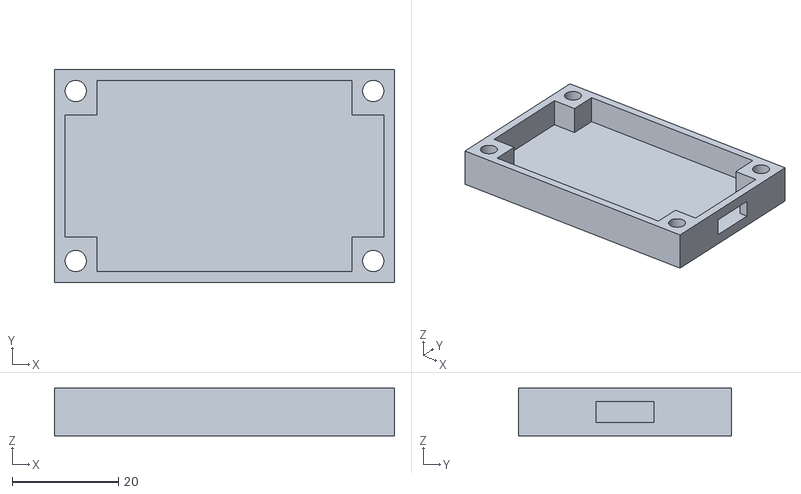
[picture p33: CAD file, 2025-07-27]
hardware/3dprinting/ProjectBoxBaseRev01.stl
64.0 x 40.0 x 9.00

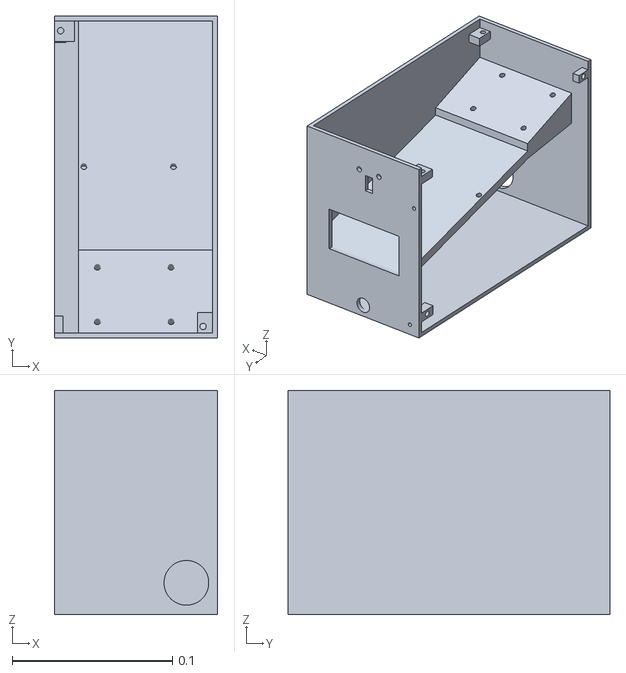
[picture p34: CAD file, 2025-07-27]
hardware/3dprinting/Case Design.stl
0.102 x 0.201 x 0.14

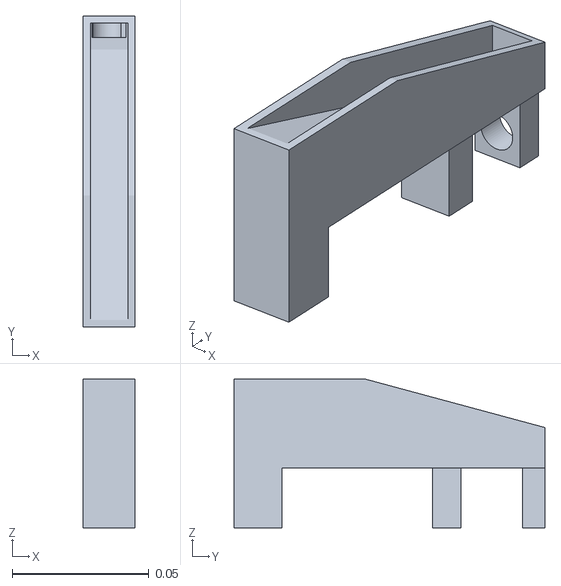
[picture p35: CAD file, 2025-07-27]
hardware/3dprinting/Resevoir 1.5.stl
0.019 x 0.114 x 0.0544

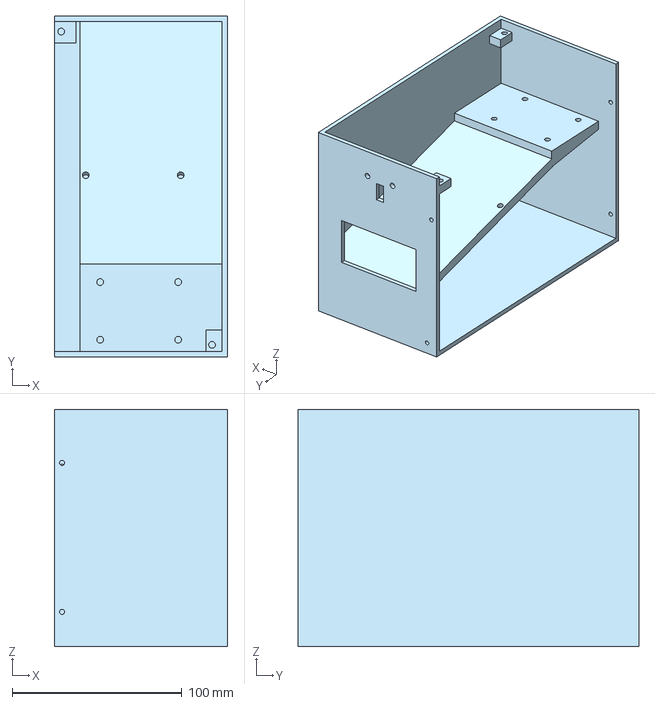
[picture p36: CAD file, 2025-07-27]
hardware/3dprinting/Part Studio 1 - Part 1.step
102.2 x 201.2 x 140.0 mm

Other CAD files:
hardware/3dprinting/openbox.scad
hardware/3dprinting/ProjectBoxBaseRev01.scad
hardware/3dprinting/Part Studio 1 - Part 1.sldprt
hardware/3dprinting/Part Studio 1 - Part 1.stl

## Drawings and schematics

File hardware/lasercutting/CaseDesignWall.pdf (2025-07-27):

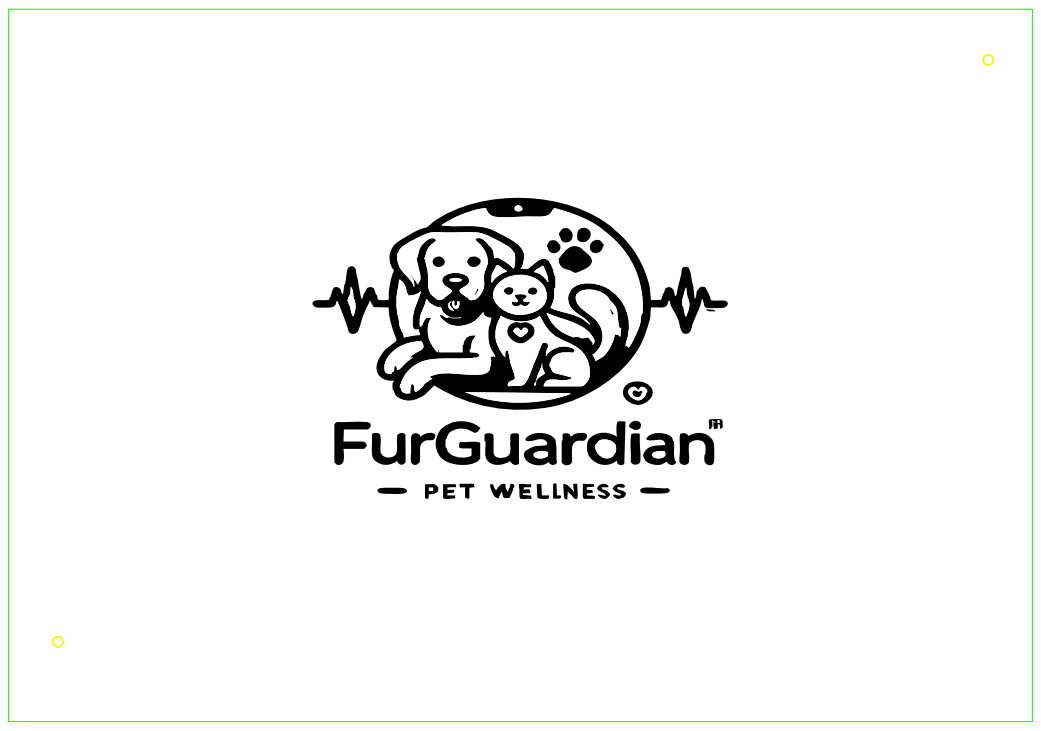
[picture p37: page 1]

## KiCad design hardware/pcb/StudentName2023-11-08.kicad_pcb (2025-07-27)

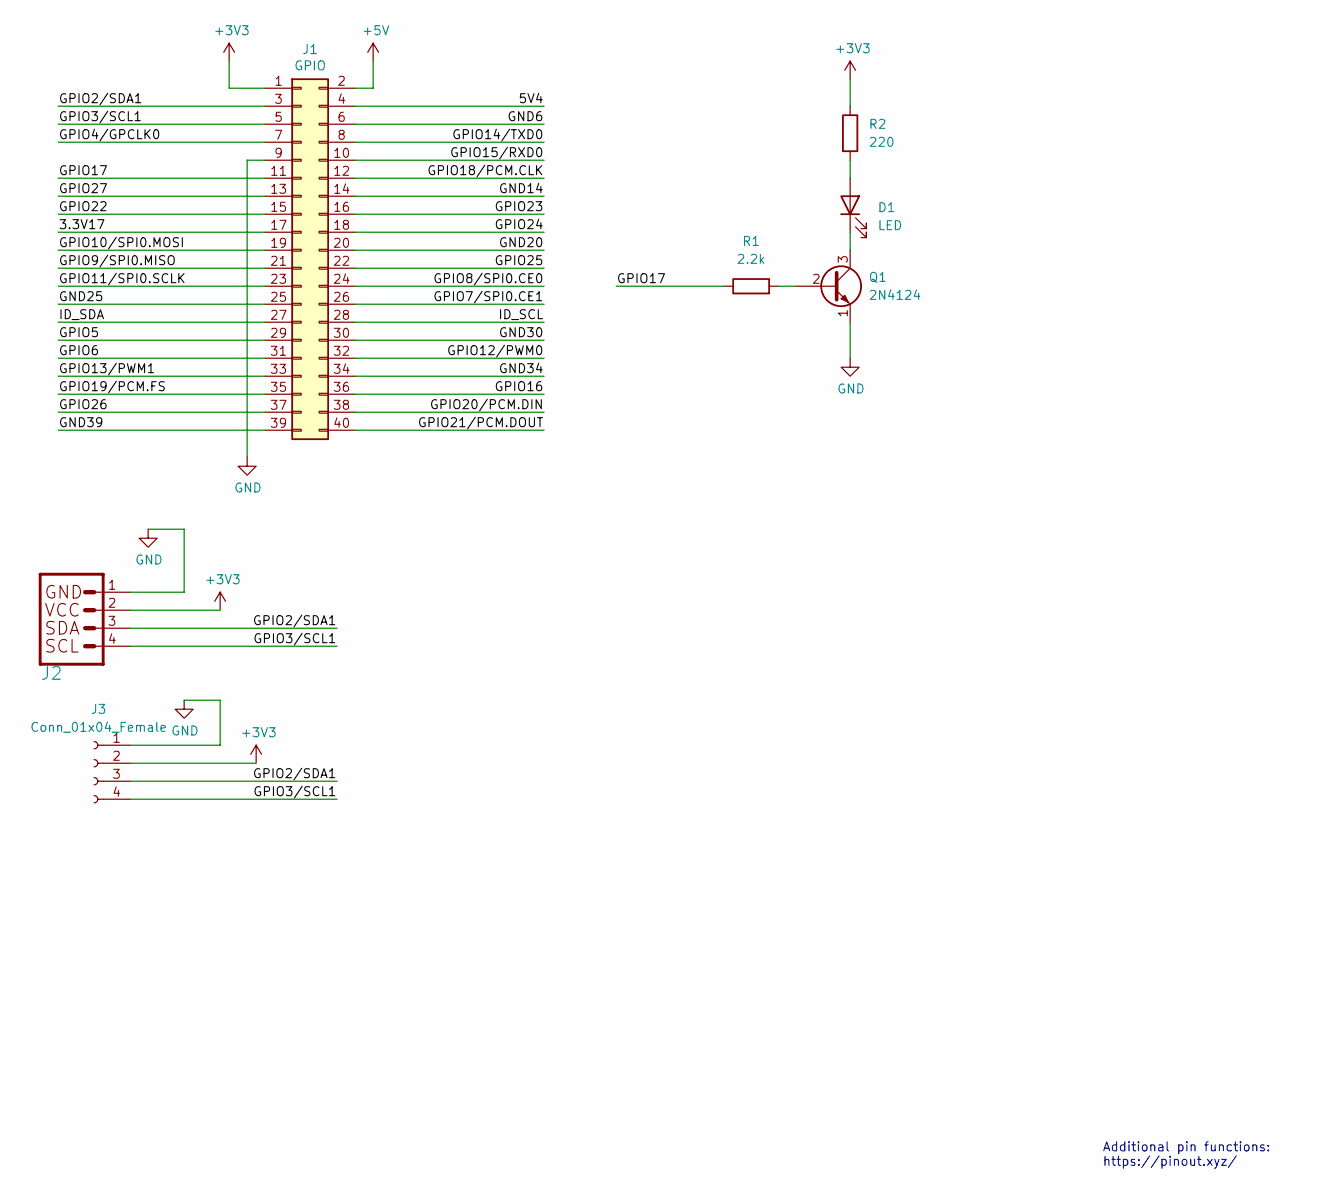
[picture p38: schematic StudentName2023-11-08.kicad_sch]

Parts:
D1: LED; LED_D5.0mm_Horizontal_O1.27mm_Z3.0mm
J1: GPIO; PinSocket_2x20_P2.54mm_Vertical
J2: Qwiic Right Angle; PinSocket_1x04_P2.00mm_Horizontal
J3: Conn_01x04_Female; PinSocket_1x04_P2.54mm_Horizontal
Q1: 2N4124; TO-92_Inline_Wide
R1: 2.2k; R_Axial_DIN0207_L6.3mm_D2.5mm_P15.24mm_Horizontal
R2: 220; R_Axial_DIN0207_L6.3mm_D2.5mm_P15.24mm_Horizontal

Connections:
+3V3: J1.1, J2.2, J3.2, R2.1
+5V: J1.2
/3.3V17: J1.17
/5V4: J1.4
/GND6: J1.6
/GND14: J1.14
/GND20: J1.20
/GND25: J1.25
/GND30: J1.30
/GND34: J1.34
/GND39: J1.39
/GPIO2/SDA1: J1.3, J2.3, J3.3
/GPIO3/SCL1: J1.5, J2.4, J3.4
/GPIO4/GPCLK0: J1.7
/GPIO5: J1.29
/GPIO6: J1.31
/GPIO7/SPI0.CE1: J1.26
/GPIO8/SPI0.CE0: J1.24
/GPIO9/SPI0.MISO: J1.21
/GPIO10/SPI0.MOSI: J1.19
/GPIO11/SPI0.SCLK: J1.23
/GPIO12/PWM0: J1.32
/GPIO13/PWM1: J1.33
/GPIO14/TXD0: J1.8
/GPIO15/RXD0: J1.10
/GPIO16: J1.36
/GPIO17: J1.11, R1.1
/GPIO18/PCM.CLK: J1.12
/GPIO19/PCM.FS: J1.35
/GPIO20/PCM.DIN: J1.38
/GPIO21/PCM.DOUT: J1.40
/GPIO22: J1.15
/GPIO23: J1.16
/GPIO24: J1.18
/GPIO25: J1.22
/GPIO26: J1.37
/GPIO27: J1.13
/ID_SCL: J1.28
/ID_SDA: J1.27
GND: J1.9, J2.1, J3.1, Q1.1 (E)
unnamed: D1.1 (K), Q1.3 (C)
unnamed: D1.2 (A), R2.2
unnamed: Q1.2 (B), R1.2

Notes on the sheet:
Additional pin functions: https://pinout.xyz/

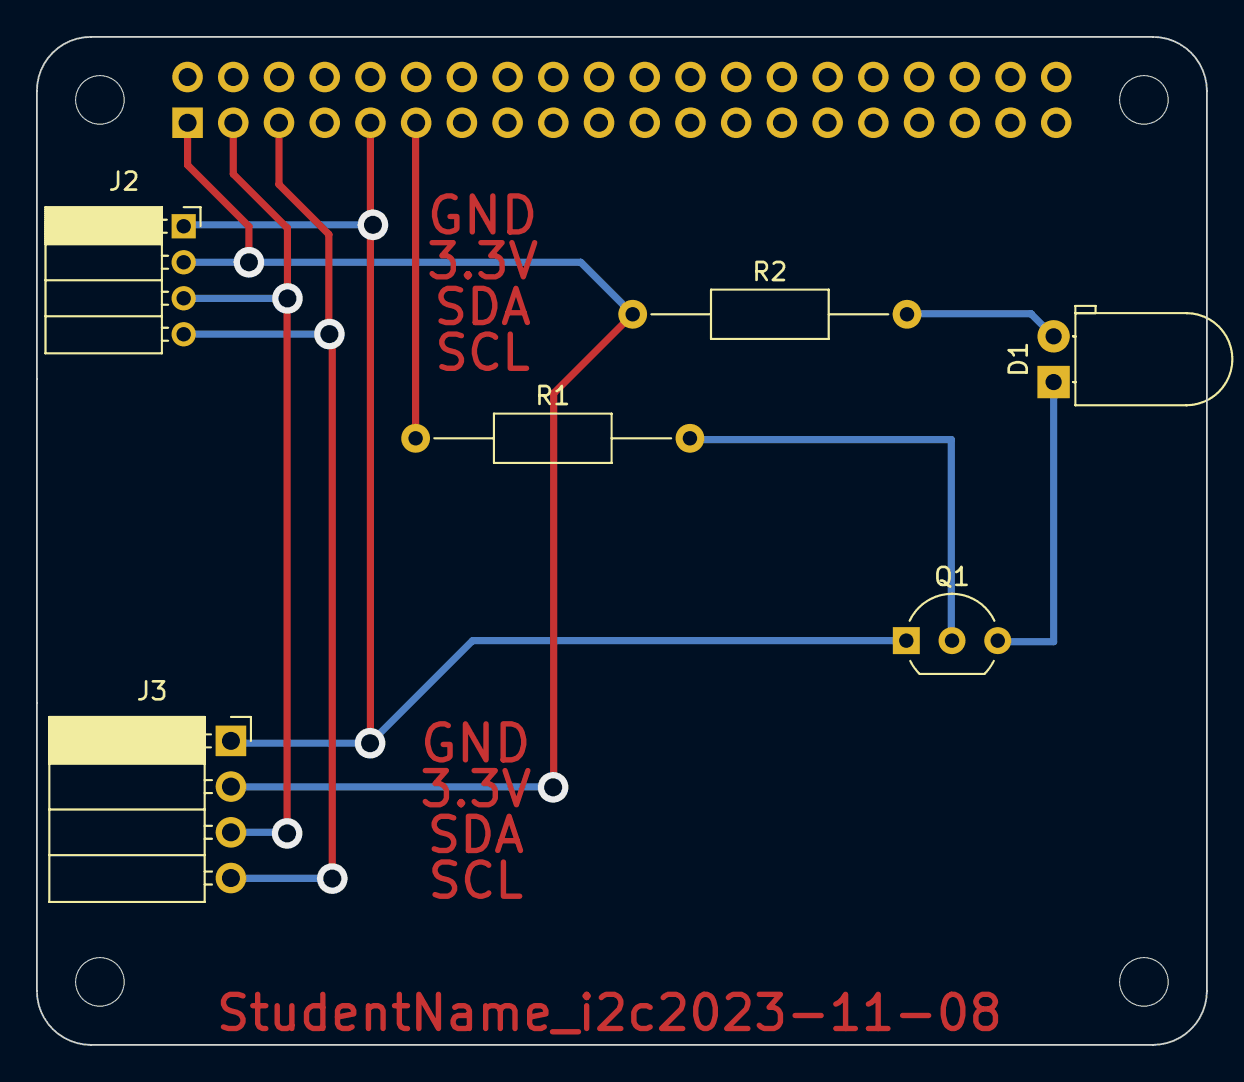
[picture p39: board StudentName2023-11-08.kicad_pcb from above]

Board: 2 copper layers, 65.0 x 56.0 mm, 11 parts (1 on the bottom side), 8 nets.

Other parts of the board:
MH1, MH2, MH3, MH4: MountingHole_2.7mm_M2.5

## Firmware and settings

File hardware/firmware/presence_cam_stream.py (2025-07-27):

#!/usr/bin/env python3
import time
import threading
import cv2
import smbus2
import qwiic_scmd
import socket
import datetime
import RPi.GPIO as GPIO
from flask import Flask, Response
from pyrebase import pyrebase
from pyngrok import ngrok

# -------------------------
# Firebase Configuration
# -------------------------
# Replace these values with your actual Firebase project configuration.
firebase_config = {
    "apiKey": "",
    "authDomain": "",
    "databaseURL": "",
    "storageBucket": ""
}

# Initialize Motor
myMotor = qwiic_scmd.QwiicScmd()
myMotor.begin()

# Initialize Firebase
firebase = pyrebase.initialize_app(firebase_config)
db = firebase.database()

# Initialize ngrok
public_url = ngrok.connect(5000, "http").public_url

R_MTR = 0  # Motor A (Coil A)
L_MTR = 1  # Motor B (Coil B)

db_date = None
last_execution_time = None  # Track when the motor last ran
COOLDOWN_SECONDS = 60      # Wait 60 seconds before allowing another run

############################
# IR Sensor Code (AK9753)
############################
LED_PIN = 17
GPIO.setmode(GPIO.BCM)
GPIO.setup(LED_PIN, GPIO.OUT)

is_human_present = False # Global flag
state_change = False # Global state change flag

class AK9753:
    AK975X_DEFAULT_ADDRESS = 0x64
    AK975X_ST1 = 0x05
    AK975X_IR1 = 0x06
    AK975X_IR2 = 0x08
    AK975X_IR3 = 0x0A
    AK975X_IR4 = 0x0C
    AK975X_ST2 = 0x10

    def __init__(self, i2c_bus=1, i2c_address=AK975X_DEFAULT_ADDRESS):
        self.bus = smbus2.SMBus(i2c_bus)
        self.address = i2c_address

    def write_register(self, register, value):
        self.bus.write_byte_data(self.address, register, value)

    def read_register(self, register, length=1):
        return self.bus.read_i2c_block_data(self.address, register, length)

    def soft_reset(self):
        # Soft-reset register
        self.write_register(0x1D, 0x01)
        time.sleep(0.1)

    def configure_sensor(self):
        # Put sensor in standby first
        self.write_register(0x1C, 0x00)
        time.sleep(0.1)
        # Set Continuous Mode 0 with cutoff frequency
        self.write_register(0x1C, 0x0C)

    def read_ir_data(self):
        ir1 = int.from_bytes(self.read_register(self.AK975X_IR1, 2), byteorder='little', signed=True)
        ir2 = int.from_bytes(self.read_register(self.AK975X_IR2, 2), byteorder='little', signed=True)
        ir3 = int.from_bytes(self.read_register(self.AK975X_IR3, 2), byteorder='little', signed=True)
        ir4 = int.from_bytes(self.read_register(self.AK975X_IR4, 2), byteorder='little', signed=True)
        # Clear DRDY
        self.read_register(self.AK975X_ST2)
        return ir1, ir2, ir3, ir4

    def check_data_ready(self):
        status = self.read_register(self.AK975X_ST1)[0]
        return (status & 0x01) != 0  # DRDY flag

def presence_monitor():
    """
    Background thread that continuously polls the IR sensor.
    If presence is detected, sets is_human_present = True,
    else False.
    """
    global is_human_present
    global state_change

    sensor = AK9753()
    sensor.soft_reset()
    sensor.configure_sensor()

    HUMAN_PRESENCE_THRESHOLD = 5000

    print("Starting IR presence monitor...")
    while True:
        if sensor.check_data_ready():
            ir1, ir2, ir3, ir4 = sensor.read_ir_data()
            max_ir = max(ir1, ir2, ir3, ir4)
            # Print debug info
            # print(f"IR Data: IR1={ir1}, IR2={ir2}, IR3={ir3}, IR4={ir4}, max={max_ir}")
            
            if max_ir > HUMAN_PRESENCE_THRESHOLD:
                GPIO.output(LED_PIN, GPIO.HIGH)
                is_human_present = True
            else:
                GPIO.output(LED_PIN, GPIO.LOW)
                is_human_present = False
            
            if state_change != is_human_present:
                update_firebase_stream_url()
                state_change = is_human_present
                

        time.sleep(0.2)

############################
# Flask + OpenCV Streaming
############################
app = Flask(__name__)

def generate_frames():
    cap = None
    while True:
        if is_human_present:
            # If camera isn't open, open it
            if cap is None or not cap.isOpened():
                cap = cv2.VideoCapture(0)
                if not cap.isOpened():
                    print("Error: Could not open camera.")
                    time.sleep(1)
                    continue

            ret, frame = cap.read()
            if not ret:
                time.sleep(0.1)
                continue

            ret, buffer = cv2.imencode('.jpg', frame)
            if not ret:
                time.sleep(0.1)
                continue

            frame_bytes = buffer.tobytes()
            yield (b'--frame\r\n'
                   b'Content-Type: image/jpeg\r\n\r\n' + frame_bytes + b'\r\n')
        else:
            # No human present: close camera if it's open
            if cap is not None:
                cap.release()
                cap = None
                print("Camera closed due to no presence.")
            break
            time.sleep(0.2)

@app.route('/video_feed')
def video_feed():
    return Response(generate_frames(),
                    mimetype='multipart/x-mixed-replace; boundary=frame')

# -------------------------
# Firebase Signaling Functions
# -------------------------

def update_firebase_stream_url():
    """
    Waits briefly, constructs the stream URL using the Pi's local IP,
    and updates Firebase with the URL under the "cameraStream" node.
    """
    global is_human_present
    global public_url
    # Wait a few seconds to allow the Flask server to start up properly.
    time.sleep(2)
    ngrok.set_auth_token("2umCIzxqWMlGyRPm3r69I8utDjo_2yFsWAco19NBKAJtXCGjM")
    
    
    stream_url = f"{public_url}/video_feed"

    
    # Update Firebase with the stream URL
    db.child("cameraStream").update({"url": stream_url})
    db.child("cameraStream").update({"stream_ready": is_human_present})
    print("Firebase updated with stream URL:", stream_url)

def motor_sequence():
    global last_execution_time
    print("Motor initialized.")
    time.sleep(0.25)

    # Zero Motor Speeds
    myMotor.set_drive(R_MTR, 0, 0)
    myMotor.set_drive(L_MTR, 0, 0)

    myMotor.enable()
    print("Motor enabled.")
    time.sleep(0.25)
    time.sleep(0.75)

    step_delay = 0.01  # Delay between steps
    steps_needed = 50  # Number of steps to make a 180-degree turn

    for step in range(steps_needed):
        myMotor.set_drive(L_MTR, 0, 254)
        time.sleep(step_delay)
        myMotor.set_drive(L_MTR, 0, 20)

        myMotor.set_drive(R_MTR, 0, 254)
        time.sleep(step_delay)
        myMotor.set_drive(R_MTR, 0, 20)

        myMotor.set_drive(L_MTR, 1, 254)
        time.sleep(step_delay)
        myMotor.set_drive(L_MTR, 1, 20)

        myMotor.set_drive(R_MTR, 1, 254)
        time.sleep(step_delay)
        myMotor.set_drive(R_MTR, 1, 20)

    # Stop the Motor
    myMotor.set_drive(R_MTR, 0, 0)
    myMotor.set_drive(L_MTR, 0, 0)
    myMotor.disable()

    # Update last execution time
    last_execution_time = time.time()

def stream_handler(message):
    global db_date
    data = message["data"]
    if data:
        print("Change Detected")
        testing = db.child("dateObject").get()
        dateData = testing.val()
        db_date = dateData.get("date", None)
        
def motor_service():
    while True:
        current_time = datetime.datetime.now().strftime("%H:%M")
    
        if db_date == current_time:
            print("inside first if")
            # Check if cooldown has passed (or if it's the first run)
            if last_execution_time is None or (time.time() - last_execution_time) >= COOLDOWN_SECONDS:
                print("inside second if")
                motor_sequence()
    
        time.sleep(1)  # Check every second


############################
# Main
############################
if __name__ == '__main__':
    # Start the IR presence monitor in a background thread
    thread = threading.Thread(target=presence_monitor, daemon=True)
    thread.start()
    
    threading.Thread(target=motor_service, daemon=True).start()

    # Start listening for database changes
    my_stream = db.child("dateObject").stream(stream_handler)

    
    #threading.Thread(target=update_firebase_stream_url, daemon=True).start();
    print("before  flask")
    # Run the Flask app on all interfaces at port 5000
    app.run(host='0.0.0.0', port=5000, threaded=True)
    print("after flask")

    

    

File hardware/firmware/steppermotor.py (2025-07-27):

import time
import sys
import qwiic_scmd

myMotor = qwiic_scmd.QwiicScmd()

def runExample():
    print("Stepper Motor Test.")
    R_MTR = 0  # Motor A (Coil A)
    L_MTR = 1  # Motor B (Coil B)

    if not myMotor.connected:
        print("Motor Driver not connected. Check connections.", file=sys.stderr)
        return

    myMotor.begin()
    print("Motor initialized.")
    time.sleep(0.25)

    # Zero Motor Speeds
    myMotor.set_drive(R_MTR, 0, 0)
    myMotor.set_drive(L_MTR, 0, 0)

    myMotor.enable()
    print("Motor enabled.")
    time.sleep(0.25)
    time.sleep(0.75)


    step_delay = .01  # Delay between steps
    steps_needed = 50  # Number of steps to make a 180-degree turn (adjust as necessary)

    for step in range(steps_needed):
        myMotor.set_drive(R_MTR, 0, 254)
        time.sleep(step_delay)
        myMotor.set_drive(R_MTR, 0, 20)

        myMotor.set_drive(L_MTR, 0, 254)
        time.sleep(step_delay)
        myMotor.set_drive(L_MTR, 0, 20)

        myMotor.set_drive(R_MTR, 1, 254)
        time.sleep(step_delay)
        myMotor.set_drive(R_MTR, 1, 20)

        myMotor.set_drive(L_MTR, 1, 254)
        time.sleep(step_delay)
        myMotor.set_drive(L_MTR, 1, 20)



    # Define the correct step sequence for a bipolar stepper motor
#    step_sequence = [
#        (255, 0),  # Step 1: Coil A forward, Coil B off
#        (255, 255),  # Step 2: Coil A forward, Coil B forward
#        (0, 255),  # Step 3: Coil A off, Coil B forward
#        (-255, 255),  # Step 4: Coil A backward, Coil B forward
#        (-255, 0),  # Step 5: Coil A backward, Coil B off
#        (-255, -255),  # Step 6: Coil A backward, Coil B backward
#        (0, -255),  # Step 7: Coil A off, Coil B backward
#        (255, -255),  # Step 8: Coil A forward, Coil B backward
#    ]
#    step_sequence = [
#        (255, 0),  # Step 1: Coil A forward, Coil B off
#        (0, 255),  # Step 3: Coil A off, Coil B forward
#        (-255, 0),  # Step 5: Coil A backward, Coil B off
#        (0, -255),  # Step 7: Coil A off, Coil B backward
#    ]
    step_sequence = [
        (255, 0),  # Ch A +
        (0, 0),  # 
        (-255, 0),  # Also A +
        (0,0),  # 
    ]

#     # Execute the steps
#     for step in range(steps_needed):
#         for phase in step_sequence:
#             # Apply each phase to the motor coils
#             coil_a_speed = abs(phase[0])
#             coil_b_speed = abs(phase[1])
#             coil_a_dir = 0 if phase[0] >= 0 else 1
#             coil_b_dir = 0 if phase[1] >= 0 else 1
# 
#             myMotor.set_drive(R_MTR, coil_a_dir, coil_a_speed)
#             myMotor.set_drive(L_MTR, coil_b_dir, coil_b_speed)
# 
#             print(f"Step: {step}, Phase: {phase}, Coil A: ({coil_a_dir}, {coil_a_speed}), Coil B: ({coil_b_dir}, {coil_b_speed})")
#             time.sleep(step_delay)

    # Stop the motor after completing the rotation
    myMotor.set_drive(R_MTR, 0, 0)
    myMotor.set_drive(L_MTR, 0, 0)
    myMotor.disable()
    print("Stepper motor test complete.")

if __name__ == '__main__':
    try:
        runExample()
    except (KeyboardInterrupt, SystemExit) as exErr:
        print("Ending example.")
        myMotor.disable()
        sys.exit(0)
